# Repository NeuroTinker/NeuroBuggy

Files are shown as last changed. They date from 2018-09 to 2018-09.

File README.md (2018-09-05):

# NeuroBuggy
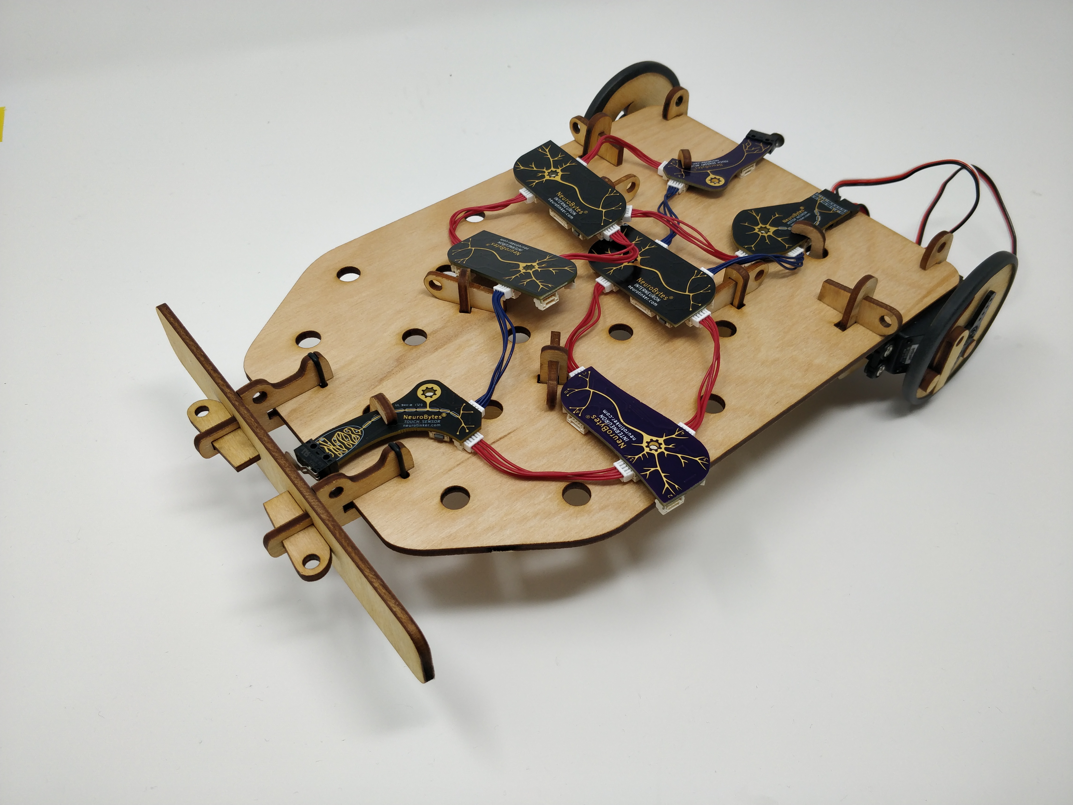
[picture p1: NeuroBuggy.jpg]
NeuroBuggy, assembled with NeuroBytes

Laser cutting files and original design documents for NeuroBuggy, our take on the Braitenberg Vehicle. Our NeuroBuggy kit will be for sale soon at https://www.neurotinker.com; until then, you should use these files and make your own. We also encourage reusing parts of our design (such as the caster mount or wedge securements); if you do this, please be sure to respect the terms of our license.

The NeuroBuggy was designed in Inkscape and is released under the terms of the Creative Commons Attribution-ShareAlike 4.0 license, available here: http://creativecommons.org/licenses/by-sa/4.0/.

## Files
```NeuroBuggy_master.svg``` is an Inkscape *.svg file that contains all of the original NeuroBuggy designs, including previous drafts. You'll see a lot in the 'layers' window, including a number of NeuroBytes boards used for sizing various bits and pieces.

```cut_file.dxf``` and ```cut_file.eps``` are two exports from the NeuroBuggy_master.svg 'parts' layer. One of them should work for your laser cutter, or just do it directly from Inkscape if you are fancy.

```instructions.pdf``` is a section from our NeuroBytes NeuroBuggy Kit manual that covers buggy construction and a few example circuits. Yes the *.pdf is large. It's because the pictures are pretty. 
## Assembly Notes
The NeuroBuggy is designed to be cut from 3mm or 1/8" plywood. The fasteners, most of which take the form of small wedges, work with a range of material thicknesses so the exact stock isn't too important. Our production kits use basswood, while some of our prototypes were made with mahogany or birch plywood. You may be able to get away with acrylic, but if you want to use plastic (gross) you probably should use something stronger like Delrin.

In addition to the wood parts, if you want to build a buggy you will need a few other bits:
* two continuous rotation hobby servos, such as SM-S4303Rs, including horns and horn mounting screws.
* a 1" plastic ball. Most materials (Delrin, polyurethane, etc) seem to work well enough.
* two O-rings for the bumper, 3/4" OD x 1/16" thickness.
* a bit of wood glue (such as Titebond III) to secure knobs to the wheels.
* two wide rubber bands, such as the type used to make lobster claws safe.

Once you have cut all the parts out, follow the instructions in the *.pdf file for assembly and (if you have a bunch of NeuroBytes boards) circuit construction.

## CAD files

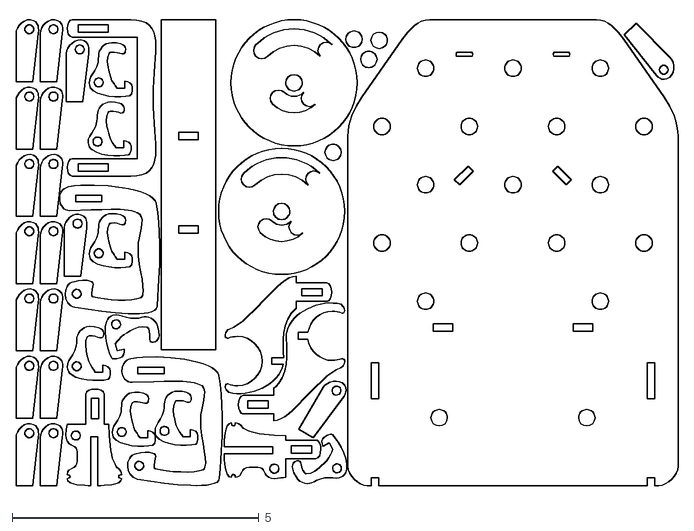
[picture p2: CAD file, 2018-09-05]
cut_file.dxf
13.4 x 9.62

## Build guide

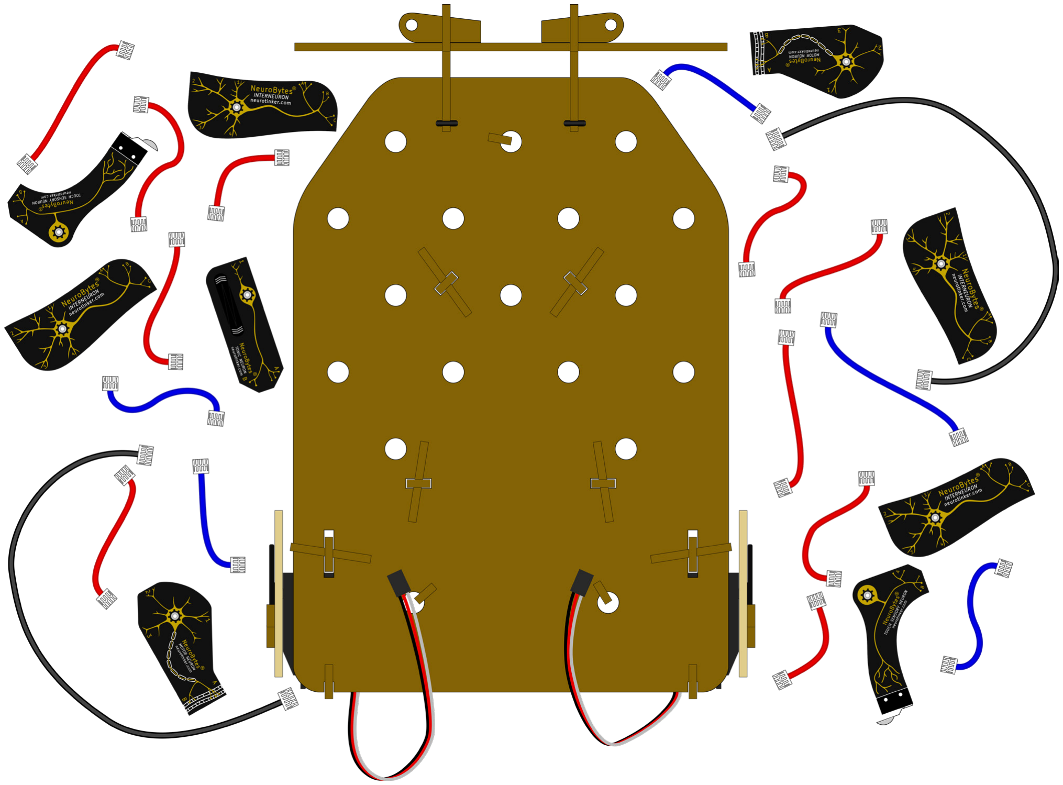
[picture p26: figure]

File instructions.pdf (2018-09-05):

# Your NeuroBuggy Kit

In 1984, the cybernetician Valentino Braitenberg published Vehicles: Experiments in Synthetic Psychology. The book, which is still available from the MIT Press, explored a series of hypothetical robots that used simple neural circuits to respond to the environment in complex ways. In many cases, these circuits may only consist of one or two processing and sensing elements, and yet a casual observer would quickly assume the robot had real feelings: fear, aggression, timidity, etc.

For many students and casual readers, Vehicles served as a first introduction into the world of neuroscience and distributed systems. However, Braitenberg never intended the constructs from the book to be built in real life; he considered the robots to be thought experiments. With the NeuroBytes NeuroBuggy Kit, you can build many of the robots from Vehicles, and extend the basic circuits presented here to create fascinating robots that can solve complex problems using relatively simple designs.

# Valentino Braitenberg’s Vehicles

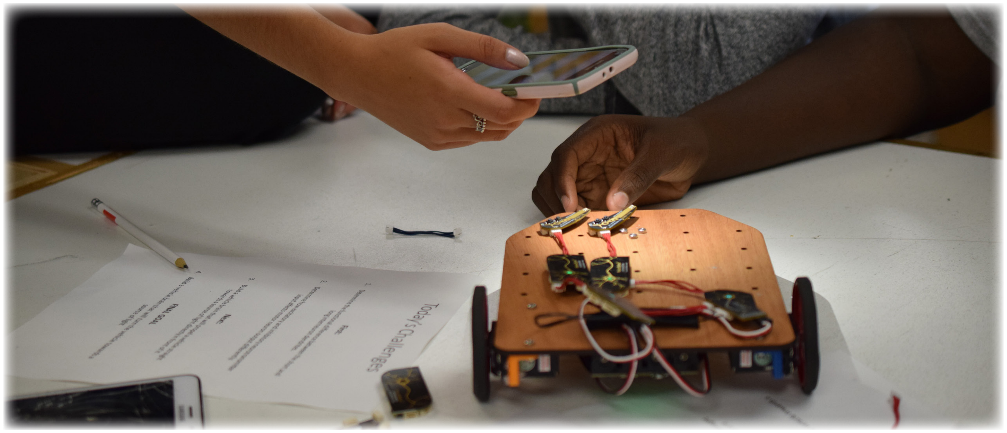
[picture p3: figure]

# Your NeuroBuggy Kit

Before building NeuroBytes circuits there are a few chassis elements you should assemble first. These wood parts can be installed in any order. Head here to see our instructional video: https://neurotinker.com/kits/neurobuggy

# Building the Neurobuggy: Front Caster

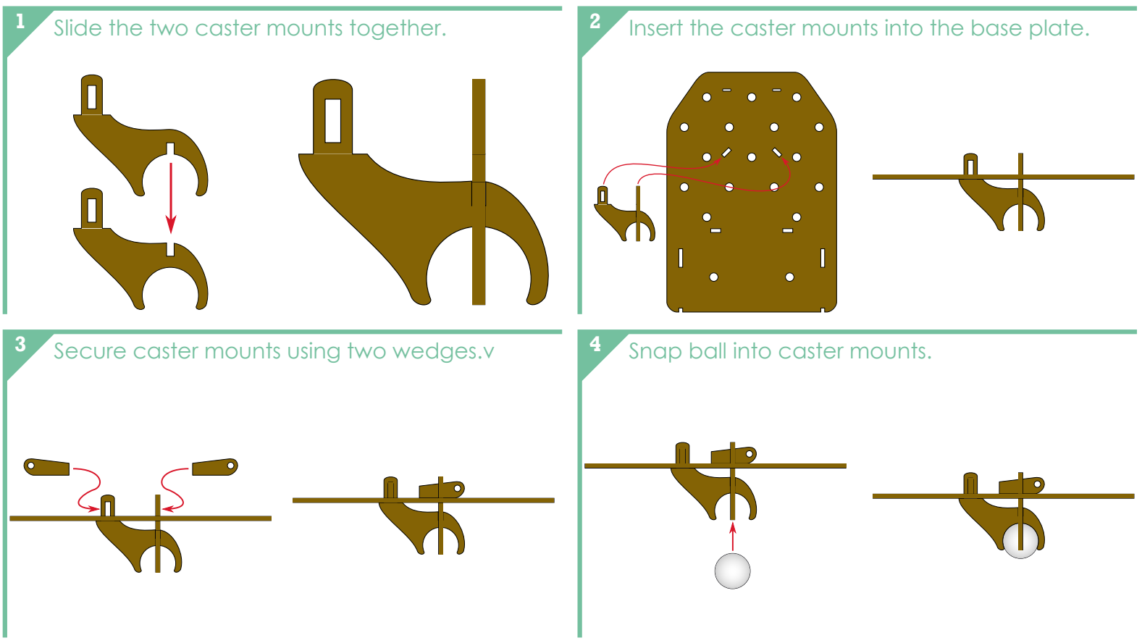
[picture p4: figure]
Slide the two caster mounts together.; Secure caster mounts using two wedges.v; Snap ball into caster mounts.

Insert the caster mounts into the base plate.

# Your NeuroBuggy Kit

Before building NeuroBytes circuits there are a few chassis elements you should assemble first. These wood parts can be installed in any order. Head here to see our instructional video: https://neurotinker.com/kits/neurobuggy

# Building the Neurobuggy: Bumper Assembly

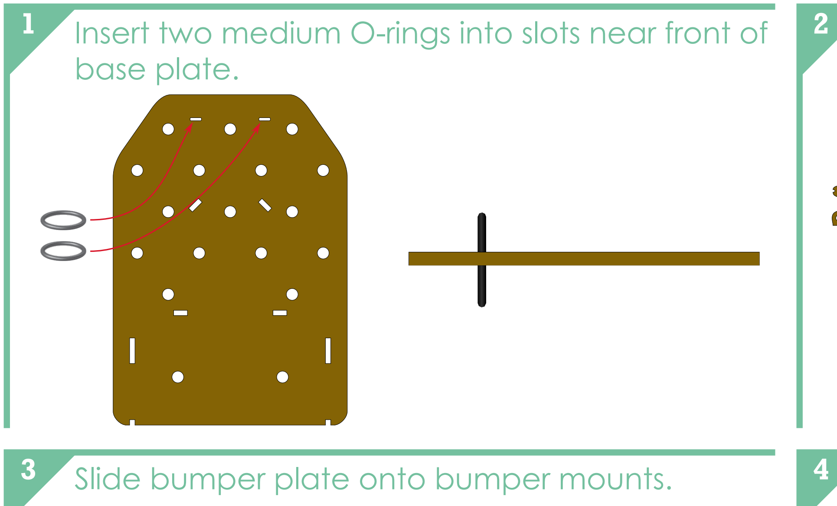
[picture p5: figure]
base plate.; Slide bumper plate onto bumper mounts.

Insert two medium O-rings into slots near front of

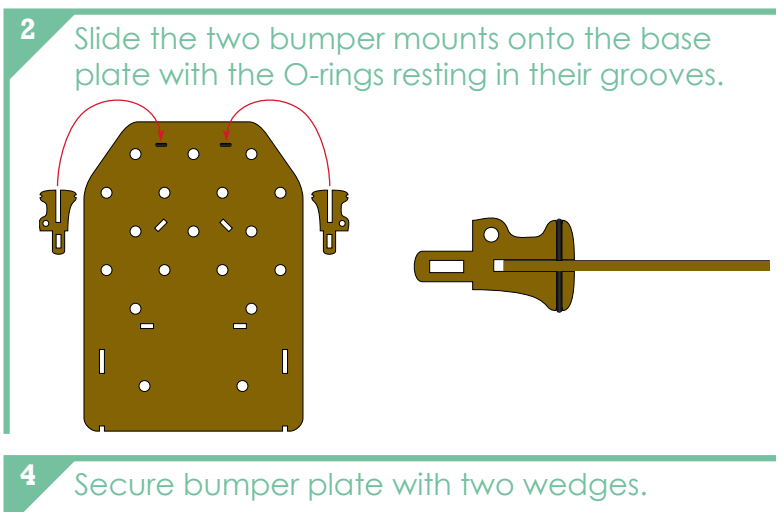
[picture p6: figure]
1` Secure bumper plate with two wedges.

Slide the two bumper mounts onto the base plate with the O-rings resting in their grooves.

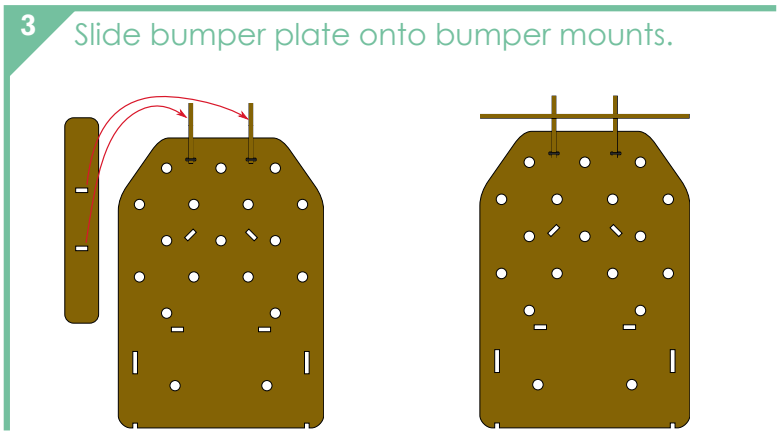
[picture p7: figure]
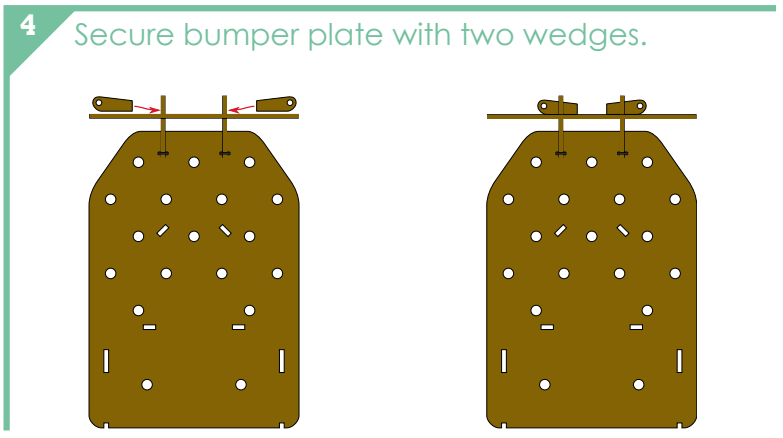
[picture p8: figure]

# Your NeuroBuggy Kit

Before building NeuroBytes circuits there are a few chassis elements you should assemble first. These wood parts can be installed in any order. Head here to see our instructional video: https://neurotinker.com/kits/neurobuggy

# Building the Neurobuggy: Servo Installation

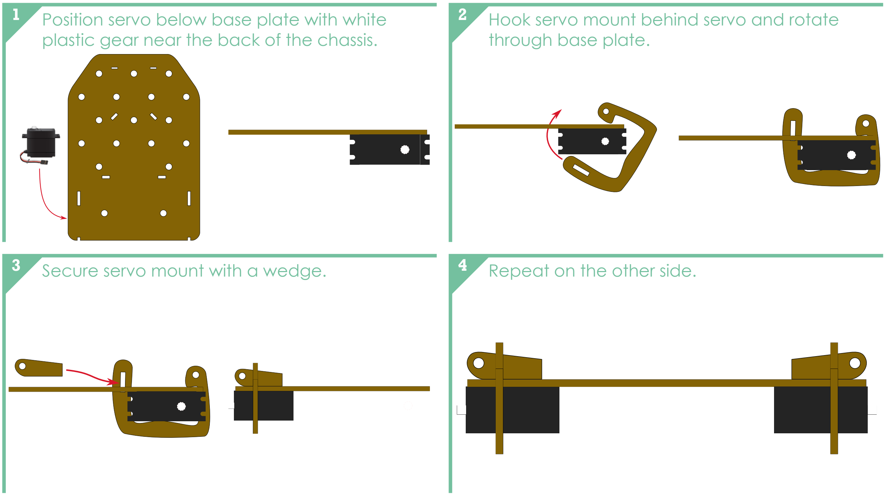
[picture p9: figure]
Secure servo mount with a wedge.; through base plate.; Repeat on the other side.

Position servo below base plate with white
plastic gear near the back of the chassis.

Hook servo mount behind servo and rotate

# Your NeuroBuggy Kit

Before building NeuroBytes circuits there are a few chassis elements you should install first. These wood subassemblies can be addressed in any order. Head here to see our instructional video: https://neurotinker.com/kits/neurobuggy

# Building the Neurobuggy: Mounting the Wheels

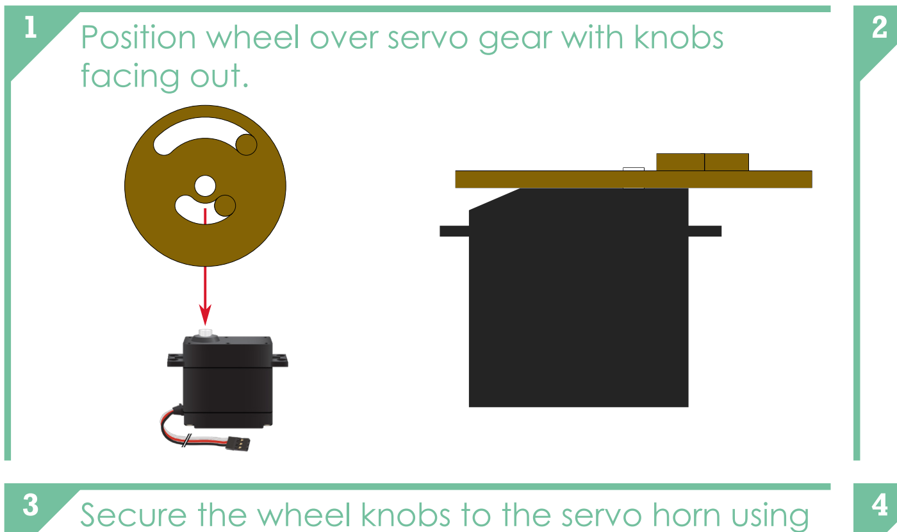
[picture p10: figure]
facing out.

Position wheel over servo gear with knobs

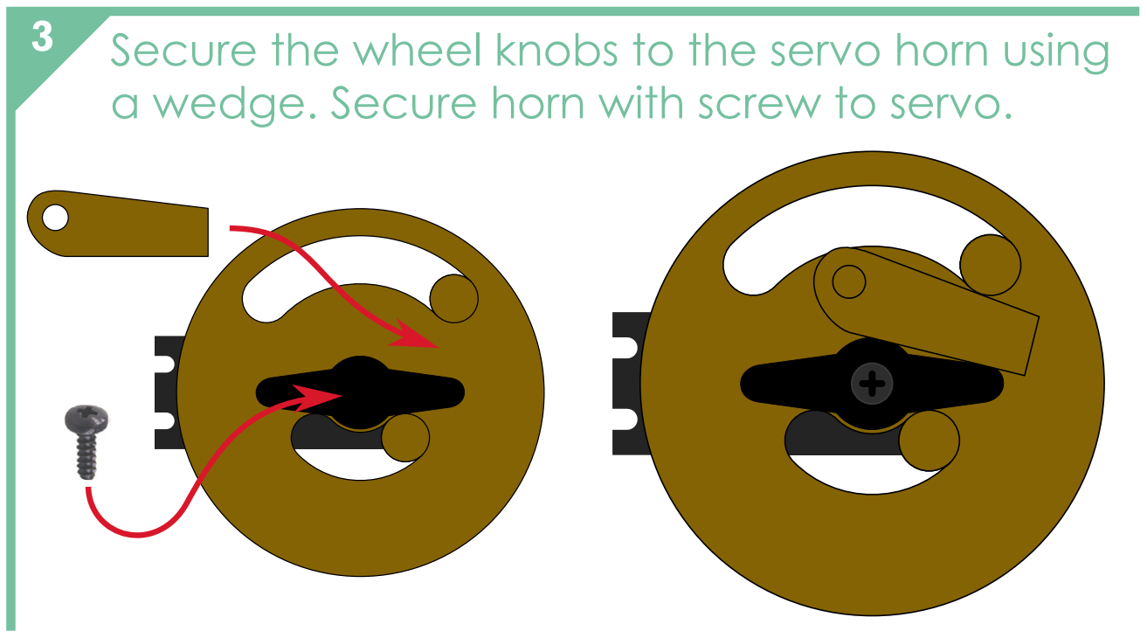
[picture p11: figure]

Secure the wheel knobs to the servo horn using a wedge. Secure horn with screw to servo.

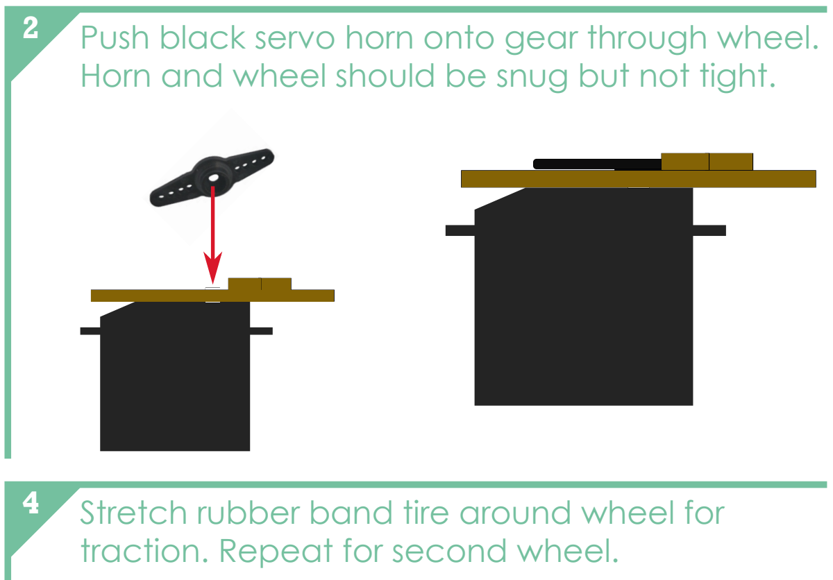
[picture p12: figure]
1` traction. Repeat for second wheel.

Push black servo horn onto gear through wheel. Horn and wheel should be snug but not tight.

Stretch rubber band tire around wheel for

# Your NeuroBuggy Kit

Before building NeuroBytes circuits there are a few chassis elements you should install first. These wood subassemblies can be addressed in any order. Head here to see our instructional video: https://neurotinker.com/kits/neurobuggy

# Building the Neurobuggy: Battery Pack

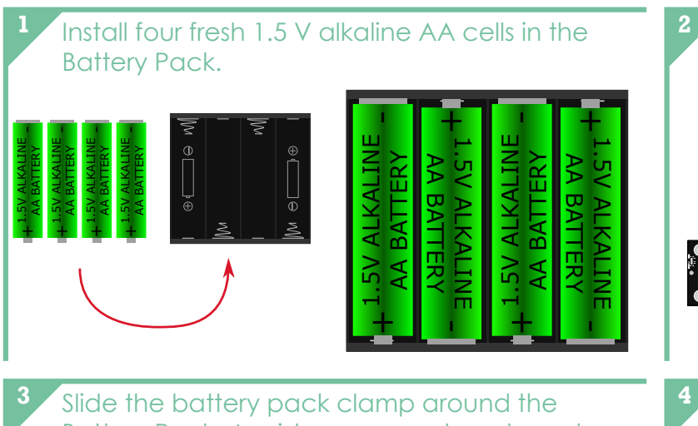
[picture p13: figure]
Battery Pack.; Slide the battery pack clamp around the; AA BATTERY; 1.5V ALKALINE

Install four fresh 1.5 V alkaline AA cells in the

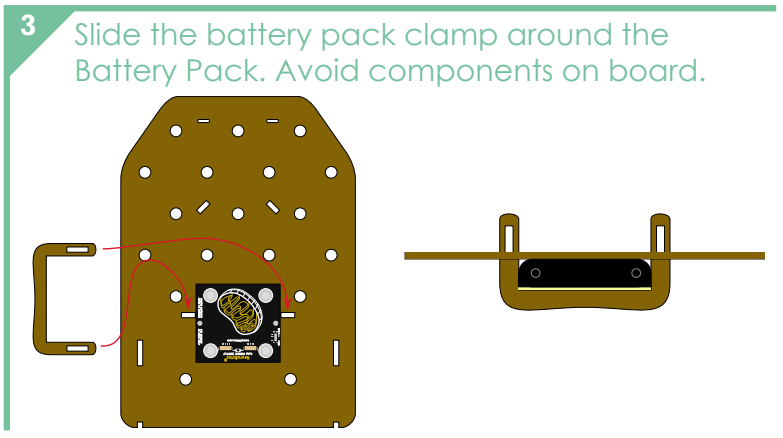
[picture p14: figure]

Battery Pack. Avoid components on board.

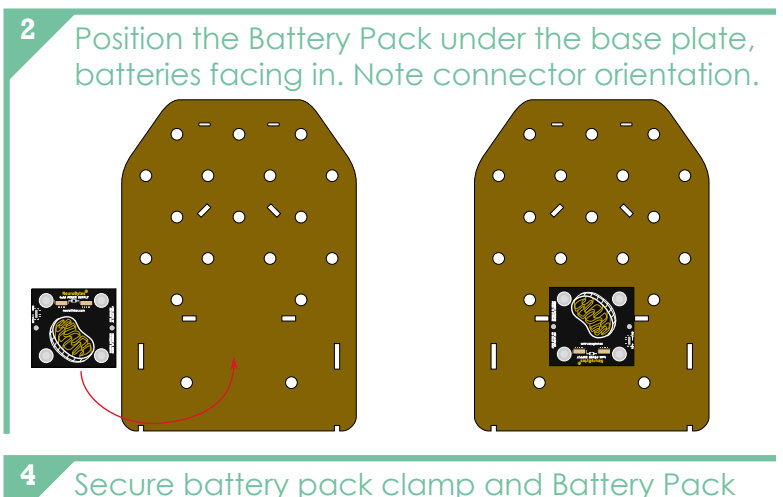
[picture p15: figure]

Position the Battery Pack under the base plate, batteries facing in. Note connector orientation.

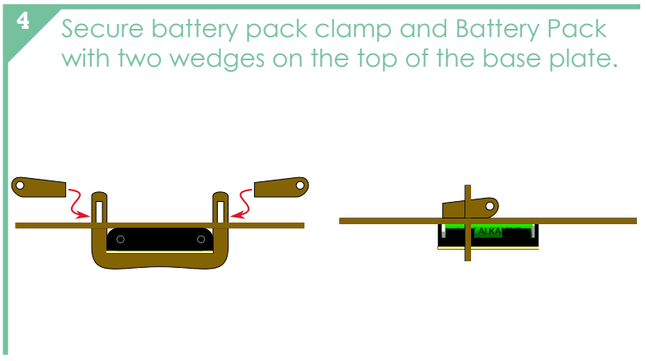
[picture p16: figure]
AA BATTERY; 1.5V ALKALINE -

Secure battery pack clamp and Battery Pack with two wedges on the top of the base plate.

# Your NeuroBuggy Kit

Before building NeuroBytes circuits there are a few chassis elements you should install first. These wood subassemblies can be addressed in any order. Head here to see our instructional video: https://neurotinker.com/kits/neurobuggy

# Building the Neurobuggy: Mounting NeuroBytes

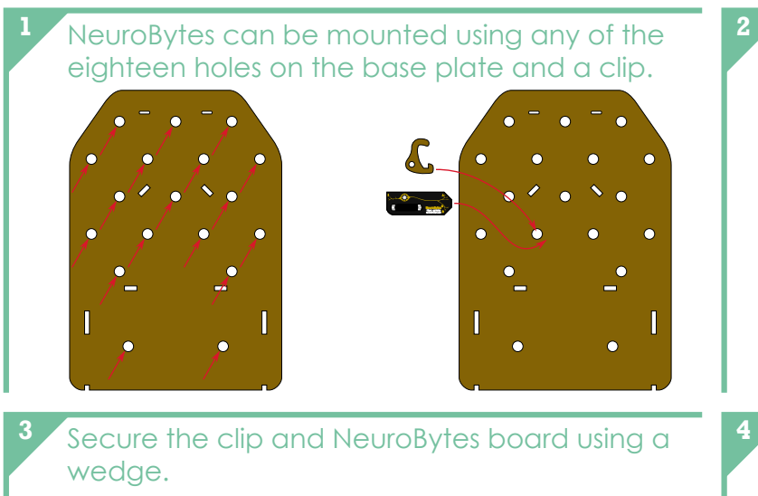
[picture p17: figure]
wedge.

NeuroBytes can be mounted using any of the
eighteen holes on the base plate and a clip.

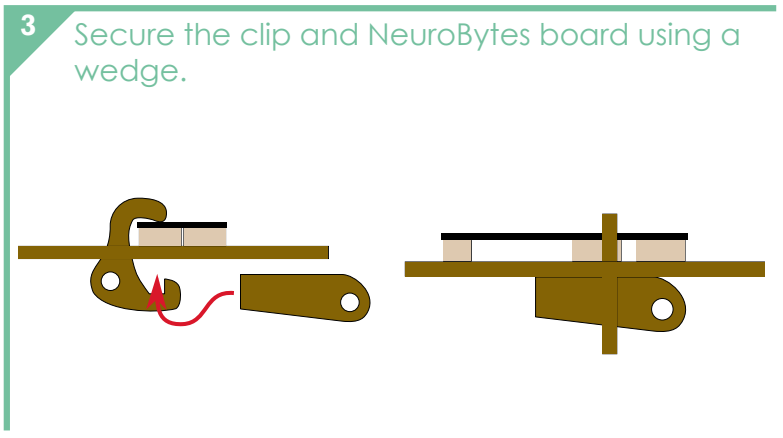
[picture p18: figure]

Secure the clip and NeuroBytes board using a

Position the NeuroBytes board near the hole.

Most NeuroBytes can’t be secured on all sides as the boards will tilt. Follow this guide.

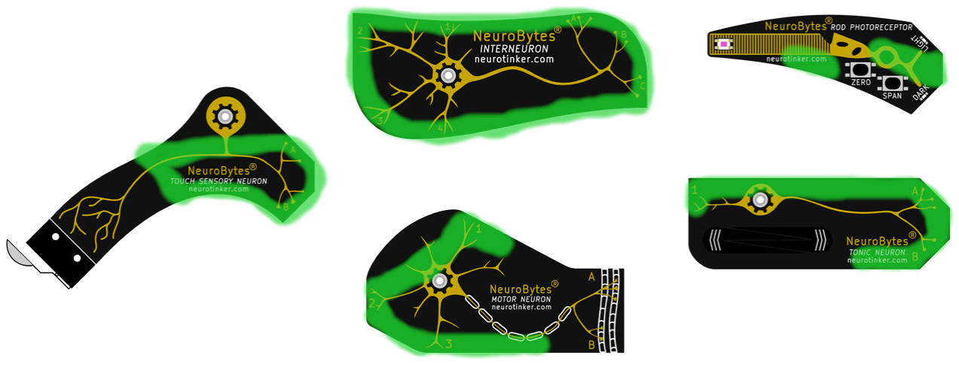
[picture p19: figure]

# Your NeuroBuggy Kit

NeuroBytes can be mounted using any of the eighteen round holes on the NeuroBuggy’s chassis, but four are particularly well-suited for their locations as shown here.

# Good Places to Mount NeuroBytes

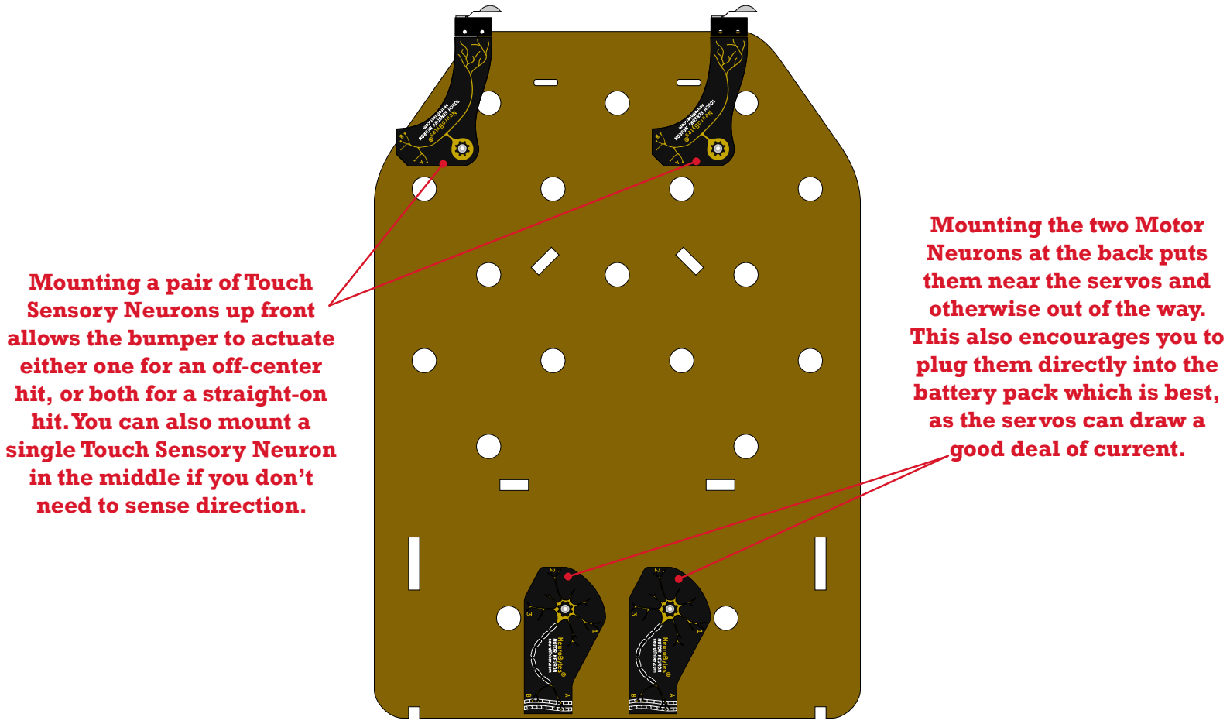
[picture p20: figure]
Mounting a pair of Touch Sensory Neurons up front allows the bumper to actuate either one for an off-center hit, or both for a straight-on hit. You can also mount a single Touch Sensory Neuron in the middle if you don’t need to sense direction.; Mounting the two Motor Neurons at the back puts them near the servos and otherwise out of the way. This also encourages you to plug them directly into the battery pack which is best, as the servos can draw a good deal of current.

# Your NeuroBuggy Kit

Timid does not like the light. With one rod photoreceptor, it senses light and drives the wheels forward when it senses light. When the photoreceptor leaves the light, the NeuroBuggy stops.

# NeuroBuggy Circuit #1: Timid

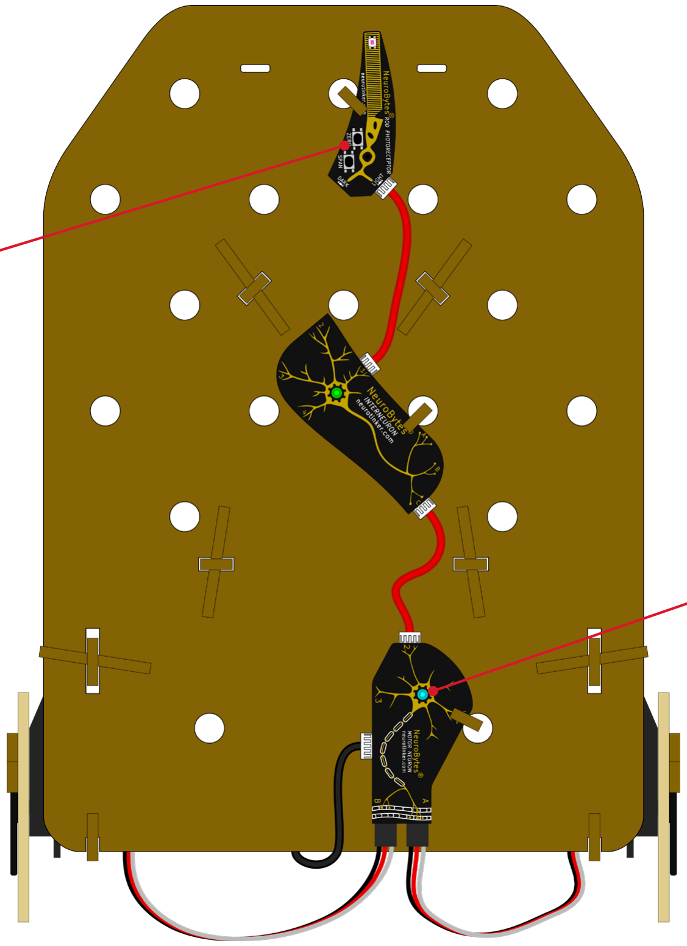
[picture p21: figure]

Zero and span the Rod
Photoreceptor for your
ambient lighting conditions.

Don’t forget to put the Motor Neuron into continuous
rotation servo mode!

# Your NeuroBuggy Kit

The Indecisive NeuroBuggy can’t make up its mind. When it’s in the light, it will drive forward until it reaches a shadow. When it reaches a shadow, it will reverse and drive back into the light.

# NeuroBuggy Circuit #2: Indecisive

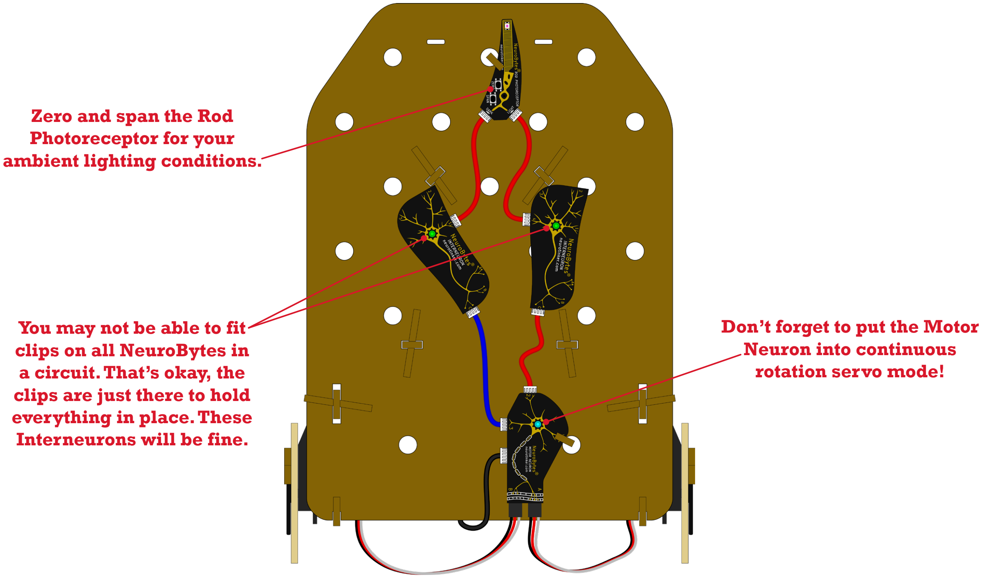
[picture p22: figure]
Zero and span the Rod Photoreceptor for your ambient lighting conditions.; You may not be able to fit clips on all NeuroBytes in a circuit. That’s okay, the clips are just there to hold everything in place. These Interneurons will be fine.; Don’t forget to put the Motor Neuron into continuous rotation servo mode!

# Your NeuroBuggy Kit

Paranoid has one rod photoreceptor that it uses to navigate its environment. It uses two interneurons and two motor neurons to do so, but the two sides of the circuit are connected a bit differently. The “light” output on the rod drives both wheels forward, while the dark output drives just the left wheel backward. This results in a NeuroBuggy that follows the edge of a light halo.

# NeuroBuggy Circuit #3: Paranoid

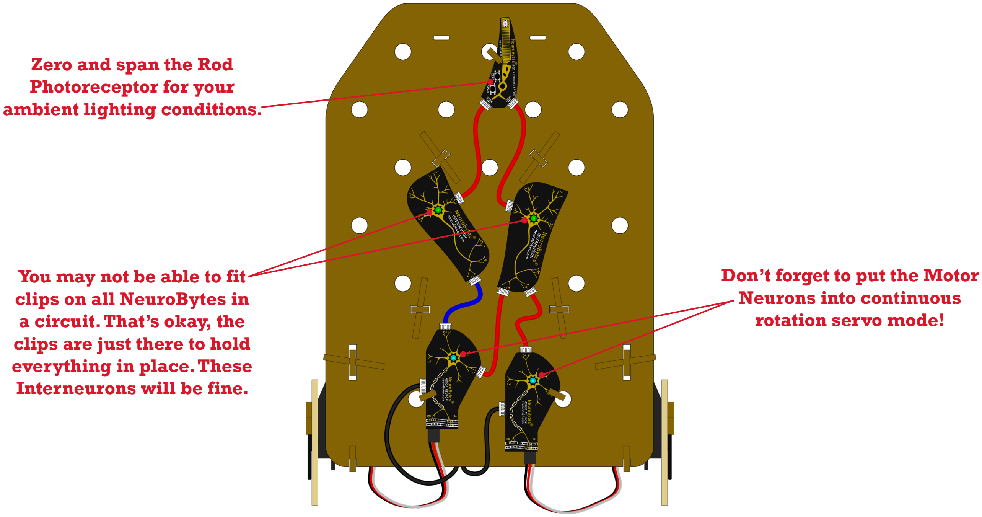
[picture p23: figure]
Zero and span the Rod Photoreceptor for your ambient lighting conditions.; You may not be able to fit clips on all NeuroBytes in a circuit. That’s okay, the clips are just there to hold everything in place. These Interneurons will be fine.; Don’t forget to put the Motor Neurons into continuous rotation servo mode!

# Your NeuroBuggy Kit

Driven is a phototropic vehicle, meaning that it moves towards the light. The connections between Interneurons and Motor Neurons are crossed from right to left, so light shone into the left Rod Photoreceptor will cause the right Motor Neuron to drive the right wheel forward, and vice versa. Can you rewire this vehicle to make it photophobic?

# NeuroBuggy Circuit #4: Driven

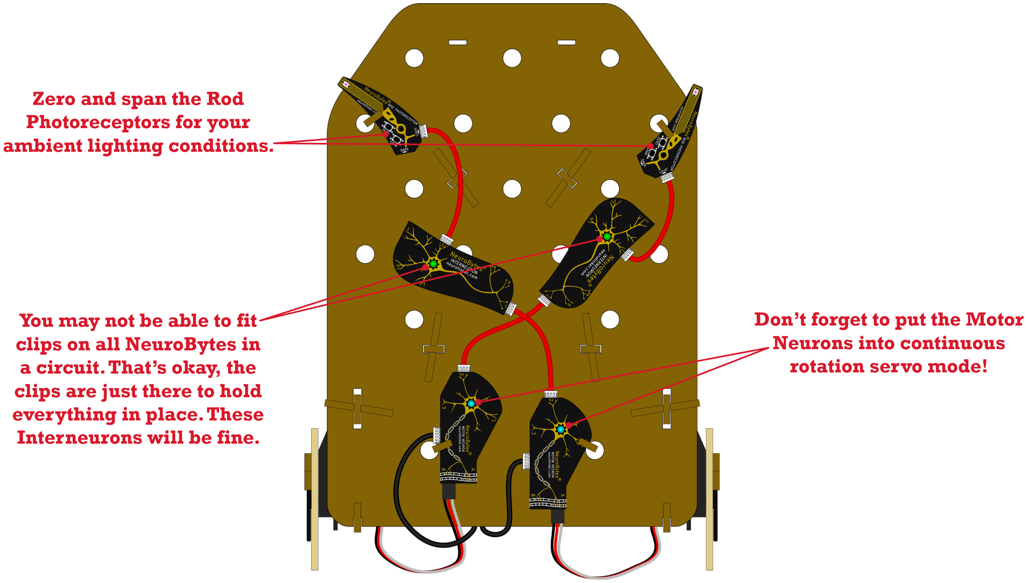
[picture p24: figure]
Zero and span the Rod Photoreceptors for your ambient lighting conditions.; You may not be able to fit clips on all NeuroBytes in a circuit. That’s okay, the clips are just there to hold everything in place. These Interneurons will be fine.; Don’t forget to put the Motor Neurons into continuous rotation servo mode!

# Your NeuroBuggy Kit

When Insecure is put down in an open area, the right wheel only will be moving forward, and the NeuroBuggy will be driving in counter-clockwise circles. If it is put down with a wall on its left however, the NeuroBuggy will move forward and left, bumping into the wall. This will activate the Touch Sensory Neuron on the left front of NeuroBuggy, which will activate the left Motor Neuron, and cause the left wheel to rotate forward. This will move the NeuroBuggy slightly away from the wall, deactivating the Touch Sensory Neuron, and the cycle begins again.

# NeuroBuggy Circuit #5: Insecure

Wall

Adjust the Tonic Neuron’s
firing rate until the
NeuroBuggy hugs the wall.

Don’t forget to put the Motor Neurons into continuous
rotation servo mode!

Make sure the Touch
Sensory Neuron is secured, but don’t overtighten
the clips. Use two clips
in two mounting holes if
necessary.

# Your NeuroBuggy Kit

Stubborn has paired two neuron oscillators on it. When the front touch sensory neuron is activated, the touch inhibits the “forward” oscillator and activates the “backwards” oscillator. When the rear touch sensory neuron is activated, the opposite happens. This circuit causes the NeuroBuggy to run back and forth between two objects.

# NeuroBuggy Circuit #6: Stubborn

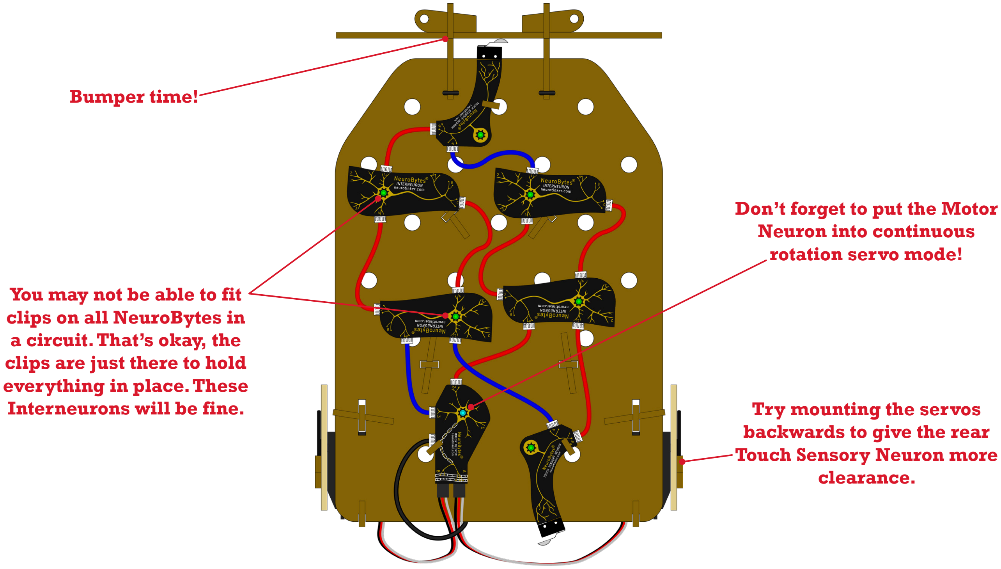
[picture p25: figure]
Bumper time!; Don’t forget to put the Motor Neuron into continuous rotation servo mode!; You may not be able to fit clips on all NeuroBytes in a circuit. That’s okay, the clips are just there to hold everything in place. These; Interneurons will be fine.; Try mounting the servos; backwards to give the rear Touch Sensory Neuron more clearance.

# Your NeuroBuggy Kit

Your NeuroBuggy kit comes with a ton of NeuroBytes, and you can even use boards from other kits on your NeuroBuggy too! See if you can incorporate all of the concepts shown before: touch and light input, independent wheel control, a Tonic Neuron heartbeat, etc. Share your projects with us, and don’t forget to name the circuit!

NeuroBuggy Circuit #7, #8, #9...

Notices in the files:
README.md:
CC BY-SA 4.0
